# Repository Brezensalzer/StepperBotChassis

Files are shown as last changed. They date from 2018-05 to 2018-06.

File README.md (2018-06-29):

# StepperBotChassis

This is the chassis of a two wheeled rover with stepper motors for 
precision movement. It is part of a larger project. The whole rover is 
"layered" in three slices:

- the chassis layer: https://github.com/Brezensalzer/StepperBotChassis
- the control layer: https://github.com/Brezensalzer/StepperBotController
- the sensor layer: https://github.com/Brezensalzer/StepperBotLidar2
- the ground station code: https://github.com/Brezensalzer/StepperBotGroundStation

The Arduino code is for a Teensy LC but should be easily adaptable to 
other microcontroller boards. Openscad, FreeCAD drawings and STL files 
are provided for 3D printing.

The chassis works great on a smooth floor (parquet) but on the seams of 
floor tiles it is easily pushed off track because of the small ball 
caster.

To complete the mechanical build, the following parts are needed:

- 2x Pololu DRV8834 Low-Voltage Stepper Motor Driver Carrier
- 2x Stepper motor 11HS12-0674S
- 2x O-rings 60 x 5 mm
- 2x 18650 LiPo cell
- LiPo protection circuit
- LiPo charging module
- Pololu ball caster 3/8" plastic ball
- Pololu 3.3V step-up/step-down voltage regulator S7V8F3
- Teensy LC
- Toggle switch 3-pin
- M2.5 screws for the stepper mounting

<p align="center">
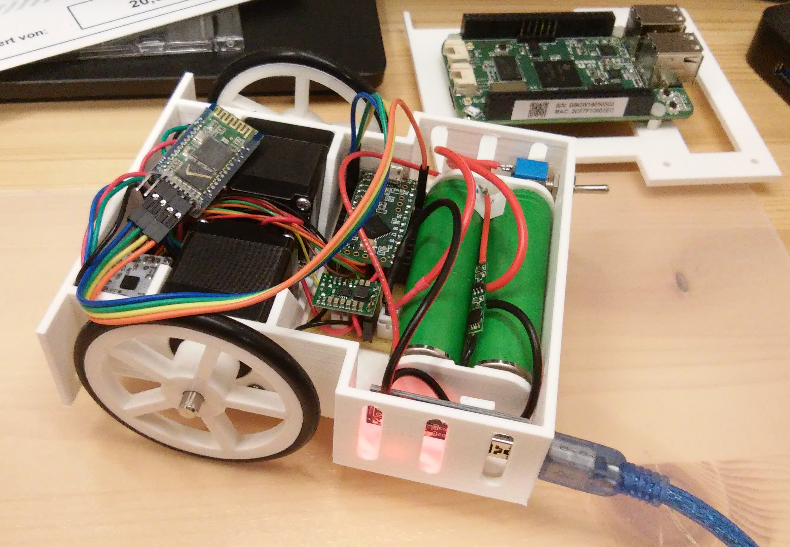
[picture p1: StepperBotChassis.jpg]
  
</p>

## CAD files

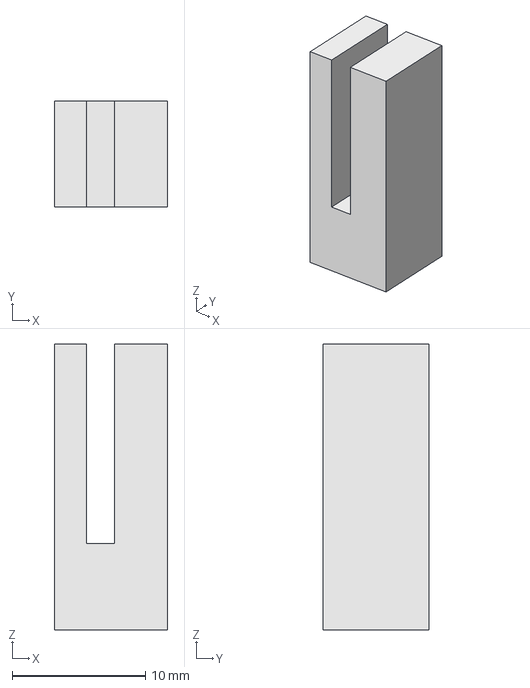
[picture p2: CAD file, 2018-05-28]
3D_parts/ChargerSockel.fcstd
8.50 x 8.00 x 21.5 mm

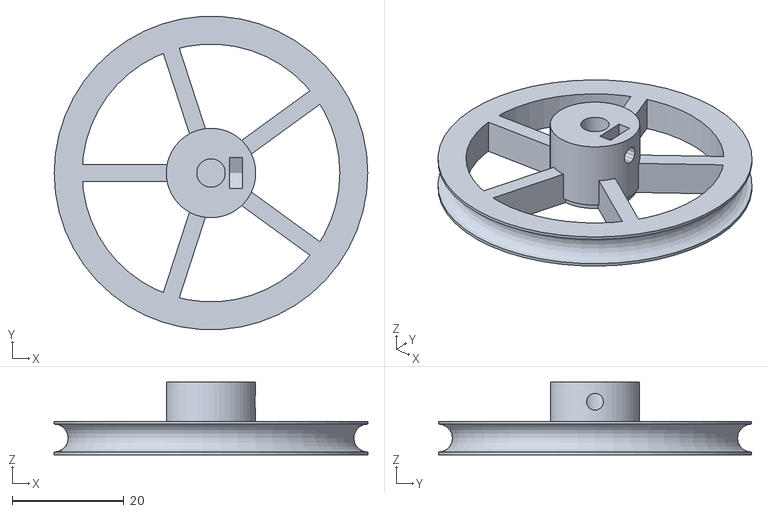
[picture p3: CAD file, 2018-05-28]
3D_parts/Wheel.stl
56.1 x 56.0 x 13.0

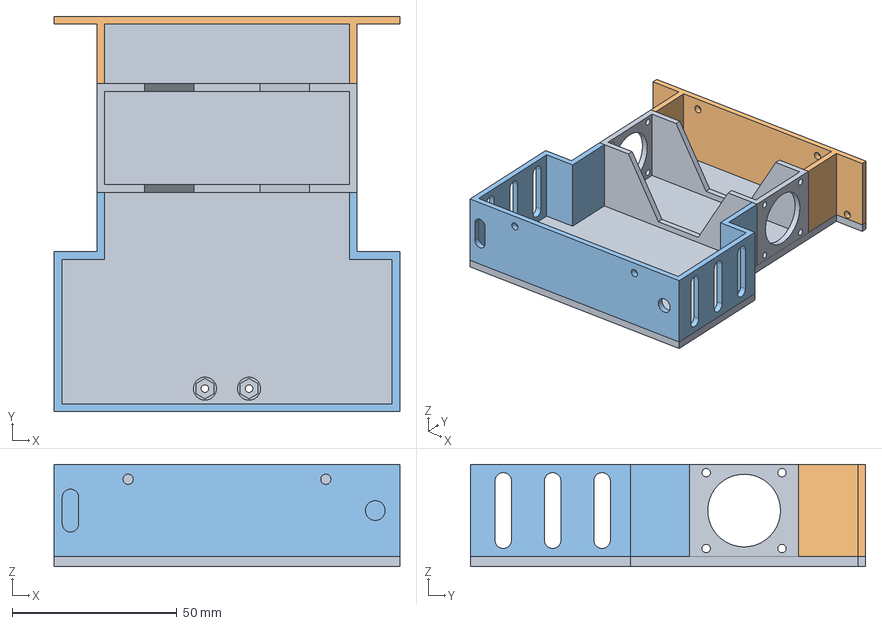
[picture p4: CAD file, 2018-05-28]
3D_parts/ChassisBase.FCStd
105.0 x 120.0 x 31.0 mm

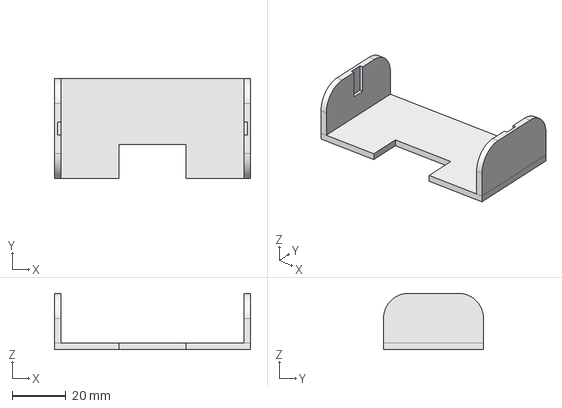
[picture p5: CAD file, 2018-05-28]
3D_parts/Batteriesockel.fcstd
72.6 x 37.0 x 20.9 mm

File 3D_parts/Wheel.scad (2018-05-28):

/*
 * Highly Configurable Wheel (One Wheel To Rule Them All)
 *
 * by Alex Franke (CodeCreations), Apr-Jun 2012
 * http://www.theFrankes.com
 * 
 * Licenced under Creative Commons Attribution - Non-Commercial - Share Alike 3.0 
 * 
 * INSTRUCTIONS: Choose some values in the "User-defined values" section, render, print, smile
 *     broadly, share with friends, and send the author a few bottles of your favorite beer. 
 * 
 * CREDITS: Center-trapped nut/bolt design inspired by Wade's Geared Extruder 
 *     (http://www.thingiverse.com/thing:1794). The spiral spoke design was apparently designed in 
 *     parallel with tjhowse's Parametric airless tire (http://www.thingiverse.com/thing:17514), and 
 *     although it can be configured to act in a very similar way, it was originally designed to be 
 *     a rigid spoke design. Vane code by JoeyC (JEC).
 *       Some features were inspired or suggested by commenters. I'll try to add credits in the code
 *     for those features. 
 * 
 * v1.33, Oct 16, 2012: Added code to generate vanes for use with slot detectors.  JEC
 * v1.32, Jun 9, 2012: Fixed a bug that cause outer nut trap to not render properly. 
 * v1.31, Jun 9, 2012: Fixed a bug that didn't include shaft flats when rendered without a hub.
 * v1.30, Jun 9, 2012: Features requested by JuliaDee: Added option for v-grooves instead of just 
 *     o-rings; Added flatted shaft option. 
 * v1.23, Apr 23, 2012: Fixed a bug that places the trapped nuts incorrectly, without considering 
 *     shaft size. Added a parameter to offset the placement of these nuts. (Thanks, AUGuru, for both 
 *     of these!) 
 * v1.22, Apr 21, 2012: Added credits section to instructions. Fixed some argument/reference issues. 
 *     Better knob foundation calculation/rendering. Fixed a number of bugs in knob sizing, including 
 *     the bug indetified by TakeItAndRun, where the knobs sometimes extend into the interior of the 
 *     wheel. 
 * v1.21, Apr 18, 2012: Fixed bug that prevented timing holes from rendering properly with spoke
 *     inset. Edited comments a bit and cleaned up some code. Combined a few parameters.
 * v1.20, Apr 17, 2012: Line style uses spokeWidth. Supports an inner circle using innerCircleDiameter. 
 *     Cleaned up some unnecessary code. Added spokeInset to allow seperate sized of rim and rest of
 *     wheel. Added captive nut option in hub. Added convexity of spoke area (inner and outer).
 * v1.10, Apr 16, 2012: Hub now supports standard hobby servo mounting arms/horns. Renders flat.
 * v1.00, Apr 15, 2012: Initial release. This is a combination of several other several other 
 *     wheel designs that all used the same framework, including http://www.thingiverse.com/thing:21277
 *     http://www.thingiverse.com/thing:21065, http://www.thingiverse.com/thing:21064, and 
 *     http://www.thingiverse.com/thing:21010, as well as some parts of my encoder wheel design at 
 *     http://www.thingiverse.com/thing:20491. I should be finishing my taxes right now. 
 *
 * TODO: 
 *   * Call wheel() with arguments (so it's more library-like)
 *   * Triangle spoke style
 *   * Gear tooth "tread" pattern
 *   * Bearing retainer (AUGuru)
 *   * perhaps move content of rim() to where the rim is actually built so inner hole can be punched out
 *   * outer hub styles (TakeItAndRun)
 */

/////////////////////////////////////////////////////////////////////////////
// User-defined values... 
/////////////////////////////////////////////////////////////////////////////

// Tire Parameters:
//      Often wheels are built around the tires. In this section, specify the properties of the 
//   tires you're using, and this will define the diameter of the wheel. If you're using o-rings, 
//   the tireCSDiameter should be the cross-section diameter of the o-ring, or if you're using some
//   other flat tire material (such as rubber bands), jsut specify the its thickness. If you're not
//   using any tire at all, set the tireCSDiameter to zero. 

wheelWidth     = 6;     // The width (or thickness) of the wheel at the rim.
tireCSDiameter = 5;     // Cross-sectional diameter (CS) -- How thick is the tire rubber?
tireID         = 50;    // Internal diameter (ID) -- How wide is the inside opening? 
tireStretch    = 1.02;  // Circumferential stretch percentage (usually 1 + 0-5%, e.g. 1.02) -- How 
                        //   much do you want to stretch it to get it on? 

// Rim properties 
//      The rim sits at at the outside of the spokes and supports the tires or added treads. 
//   Installed tires (such as o-rings, rubber bands, etc) are set into grooves carved out of the
//   rim, while trads are added onto it. Keep this in mind when you're using tires -- as an 
//   example, the rim height should not be smaller than the radius of o-ring tires. 
//      The rim also supports rotary encoder timing holes for wheel feedback. Use the padding 
//   parameters to adjust the location of those holes. See the compiler output for helpful 
//   information about the distance indicated by each timing hole. Directional timing holes 
//   will produce a second set of holes that are 90 degrees out of phase with the first. This 
//   allows you to stack sensors at the same location over the wheel instead of trying to 
//   position them along the circumference. Directional timing holes essentially double the 
//   resolution. You can also double resolution by looking for both rising and falling edges. 

rimHeight      = 5;        // The height of the rim portion of the wheel. 
timingHoles    = 0;        // The number of timing holes to carve into the rim
timingHolePad  = [1,0.5,3]; // The [inside,middle,outside] padding for the timing holes
directional    = false;      // A directional encoder renders two sets of slots, 90 deg out of phase

// Added 10/16/2012 JEC
// Slot detector vane properties
// These settings generate small vanes on the inside of the rim for use with
// IR slot detectors that are too narrow to be put over the wheel.
vaneCount		= 0;			// Number of slot detector vanes to put inside rim
vaneHeight		= 7;			// The height of the vanes
vaneWidth		= 1;			// Width of vanes
vaneLength		= 4;			// Length of vanes
vaneOffset		= 1;			// Offset into wheel of vanes
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

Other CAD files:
3D_parts/Batteriesockel.stl
3D_parts/ChargerSockel.stl
3D_parts/ChassisBase.stl

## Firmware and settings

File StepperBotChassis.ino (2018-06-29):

// StepperBotChassis.ino
//
//    Wiring
//
//    Function          Teensy LC             Beaglebone green
//    ---------------   ---------------       -----------------
//    serial            Pin 0 (RX1)           P9-13 (UART4_TXD)
//    serial            Pin 1 (TX1)           P9-11 (UART4_RXD)
//    emergency break   Pin 3 (Input, pullup) P9-15 (GPIO_48, Output)
//    DRV8834 sleep     Pin 4 (Output)        -
//    M0 Microstepping  Pin 5 (Output)        -
//    M1 Microstepping  Pin 6 (Output)        -
//    step right        Pin 7 (Output)        -
//    dir right         Pin 8 (Output)        -
//    step left         Pin 9 (Output)        -
//    dir left          Pin 10 (Output)       -

#include <AccelStepper.h>
#include <MultiStepper.h>

// sleep/enable pin
#define SLEEP_PIN 4
// microstep control for DRV8834
#define M0 5
#define M1 6
// All the wires needed for full functionality
#define STEP_RIGHT 7
#define DIR_RIGHT 8
#define STEP_LEFT 9
#define DIR_LEFT 10
#define EMERGENCY_PIN 3

// global variables
int   stepperSpeed = 400;   // speed of the stepper (steps per second)
float wheel_dia = 61.0;      // # mm (increase = spiral out)
float wheel_base = 105.2;    // # mm (increase = spiral in) 
int   steps_rev = 200;      // steps per revolution
long positions[2];
long steps1, steps2, delta;
int gear = 1;
   
// Serial Com
const char del = '#';     // delimiter
int  num;           // bytes received
char cmd;           // command
int  cmdFloat;      // command value as float
String command;

AccelStepper stepperLeft(AccelStepper::DRIVER, STEP_LEFT, DIR_LEFT);
AccelStepper stepperRight(AccelStepper::DRIVER, STEP_RIGHT, DIR_RIGHT);

// Up to 10 steppers can be handled as a group by MultiStepper
MultiStepper steppers;

void setup() {
  // serial com
  Serial1.begin(9600);
  Serial1.flush();
  Serial1.setTimeout(10000); 
  
  // set power on/off pin
  stepperLeft.setEnablePin(SLEEP_PIN);
  stepperRight.setEnablePin(SLEEP_PIN);

  //set target motor speed steps/s.
  stepperLeft.setMaxSpeed(stepperSpeed);
  stepperRight.setMaxSpeed(stepperSpeed);
  
  // set full steps and enable driver
  // M0 = low, M1 = low
  pinMode(M0, OUTPUT);
  digitalWrite(M0, LOW);
  pinMode(M1, OUTPUT);
  digitalWrite(M1, LOW);
  pinMode(SLEEP_PIN, OUTPUT);
  digitalWrite(SLEEP_PIN, HIGH);

  // Then give them to MultiStepper to manage
  steppers.addStepper(stepperLeft);
  steppers.addStepper(stepperRight);

  // energy saving
  enableOutput(false);

  // emergency stop
  pinMode(EMERGENCY_PIN, INPUT_PULLUP);
}

void loop() {
  // reset variables
  command = "";
  num = 0;
  cmd = 'X';

  // read and parse command
  command = Serial1.readStringUntil(del);
  
  if (command != "") {
    cmd = command.charAt(0);
    num = command.indexOf(del);
    command = command.substring(1,num);
    cmdFloat = command.toFloat();

    // execute command
    switch (cmd) {
      // enable output
      case 'e':
        enableOutput(true);
        break;
      // disable output
      case 'd':
        enableOutput(false);
        break;
      // forward
      case 'f':
        forward(cmdFloat);
        break;
      // backward
      case 'b':
        backward(cmdFloat);
        break;
      // turn left
      case 'l':
        left(cmdFloat);
        break;
      // turn right
      case 'r':
        right(cmdFloat);
        break;
      // set stepper speed
      case 's':
        stepperSpeed = command.toInt();
        break;
      // set wheel diameter
      case 'w':
        wheel_dia = cmdFloat;
        break;
      // set wheel track width
      case 't':
        wheel_base = command.toFloat();
        break;
      // debug info
      case 'i':
        Serial1.println("$Id$");
        Serial1.print("wheel diameter: ");
        Serial1.println(wheel_dia);
        Serial1.print("wheel_base: ");
        Serial1.println(wheel_base);
        Serial1.print("stepperSpeed: ");
        Serial1.println(stepperSpeed);
        break;
      default:
        Serial1.println("error");
        break;
      }
    Serial1.println("ok");
    Serial1.flush(); 
  }
  
}

// ----- HELPER FUNCTIONS -----------
int step(float distance){
  int steps = distance * steps_rev / (wheel_dia * 3.1412);
  //Serial1.print("calculated steps: ");
  //Serial1.println(steps);
  return steps;  
}

void enableOutput(boolean flag){
  if(flag){
    // wakeup steppers
    stepperLeft.enableOutputs();
    stepperRight.enableOutputs();    
  }
  else{
    // energy saving
    stepperLeft.disableOutputs();
    stepperRight.disableOutputs();    
  }
}

void emergencyStop(){
  if(digitalRead(EMERGENCY_PIN) == LOW){
    stepperLeft.stop();  
    stepperRight.stop();
  }
}

void forward(float distance){
  gear = 1;
  positions[0] = step(distance);  
  positions[1] = positions[0];
  steps1 = positions[0];
  steppers.moveTo(positions);
  stepperLeft.setSpeed(stepperSpeed/4);
  stepperRight.setSpeed(-stepperSpeed/4);
  while (steps1 > 0) {
    emergencyStop();
    steps1 = stepperLeft.distanceToGo();
    steps2 = stepperRight.distanceToGo();
    // poor man's acceleration
    delta = positions[0] - steps1;
    if ((delta >= 10) && (delta < 50))
      {
        if (gear == 1) {
          stepperLeft.setSpeed(stepperSpeed/2);
          stepperRight.setSpeed(-stepperSpeed/2);
          gear = 2;
        }
       }
    else if ((delta >= 50) && (steps1 > 50))  
      {
        if (gear == 2) {
          stepperLeft.setSpeed(stepperSpeed*3/4);
          stepperRight.setSpeed(-stepperSpeed*3/4);
          gear = 3;
        }
       }
    else if ((delta >= 100) && (steps1 > 100))  
      {
        if (gear == 3) {
          stepperLeft.setSpeed(stepperSpeed);
          stepperRight.setSpeed(-stepperSpeed);
          gear = 4;
        }
       }
    // deceleration   
    else if ((steps1 <= 100) && (steps1 > 50))   
      {
        if (gear == 4) {
          stepperLeft.setSpeed(stepperSpeed/2);
          stepperRight.setSpeed(-stepperSpeed/2);
          gear = 3;
        }
       }
    else if ((steps1 <= 50) && (steps1 > 10))   
      {
        if (gear == 3) {
          stepperLeft.setSpeed(stepperSpeed/2);
          stepperRight.setSpeed(-stepperSpeed/2);
          gear = 2;
        }
       }
    else if (steps1 <= 10)   
      {
        if (gear == 2) {
          stepperLeft.setSpeed(stepperSpeed/4);
          stepperRight.setSpeed(-stepperSpeed/4);
          gear = 1;
        }
       }
    steppers.run();
  }
  stepperLeft.setCurrentPosition(0);
  stepperRight.setCurrentPosition(0);
}

void backward(float distance){
  gear = 1;
  positions[1] = step(distance);  
  positions[0] = positions[1];
  steps2 = positions[1];
  steppers.moveTo(positions);
  stepperLeft.setSpeed(-stepperSpeed/4);
  stepperRight.setSpeed(stepperSpeed/4);
  while (steps2 > 0) {
    emergencyStop();
    steps1 = stepperLeft.distanceToGo();
    steps2 = stepperRight.distanceToGo();
    // poor man's acceleration
    delta = positions[1] - steps2;
    if ((delta >= 10) && (delta < 50))
      {
        if (gear == 1) {
          stepperLeft.setSpeed(-stepperSpeed/2);
          stepperRight.setSpeed(stepperSpeed/2);
          gear = 2;
        }
       }
    else if ((delta >= 50) && (steps2 > 50))  
      {
        if (gear == 2) {
          stepperLeft.setSpeed(-stepperSpeed*3/4);
          stepperRight.setSpeed(stepperSpeed*3/4);
          gear = 3;
        }
       }
    else if ((delta >= 100) && (steps2 > 100))  
      {
        if (gear == 3) {
          stepperLeft.setSpeed(-stepperSpeed);
          stepperRight.setSpeed(stepperSpeed);
          gear = 4;
        }
       }
    // deceleration   
    else if ((steps2 <= 100) && (steps2 > 50))   
      {
        if (gear == 4) {
          stepperLeft.setSpeed(-stepperSpeed/2);
          stepperRight.setSpeed(stepperSpeed/2);
          gear = 3;
        }
       }
    else if ((steps2 <= 50) && (steps2 > 10))   
      {
        if (gear == 3) {
          stepperLeft.setSpeed(-stepperSpeed/2);
          stepperRight.setSpeed(stepperSpeed/2);
          gear = 2;
        }
       }
    else if (steps2 <= 10)   
      {
        if (gear == 2) {
          stepperLeft.setSpeed(-stepperSpeed/4);
          stepperRight.setSpeed(stepperSpeed/4);
          gear = 1;
        }
       }
    steppers.run();
  }
  stepperLeft.setCurrentPosition(0);
  stepperRight.setCurrentPosition(0);
}

void right(float degrees){
  float rotation = degrees / 360.0;
  float distance = wheel_base * 3.1412 * rotation;
  positions[0] = step(distance);  
  positions[1] = positions[0];
  steps1 = positions[0];
  steppers.moveTo(positions);
  stepperLeft.setSpeed(stepperSpeed/4);
  stepperRight.setSpeed(stepperSpeed/4);
  while (steps1 > 0) {
    steps1 = stepperLeft.distanceToGo();
    steps2 = stepperRight.distanceToGo();
    steppers.run();
  }
  stepperLeft.setCurrentPosition(0);
  stepperRight.setCurrentPosition(0);
}

void left(float degrees){
  float rotation = degrees / 360.0;
  float distance = wheel_base * 3.1412 * rotation;
  positions[0] = -step(distance);  
  positions[1] = positions[0];
  steps1 = positions[0];
  steppers.moveTo(positions);
  stepperLeft.setSpeed(-stepperSpeed/4);
  stepperRight.setSpeed(-stepperSpeed/4);
  while (abs(steps1) > 0) {
    steps1 = stepperLeft.distanceToGo();
    steps2 = stepperRight.distanceToGo();
    steppers.run();
  }
  stepperLeft.setCurrentPosition(0);
  stepperRight.setCurrentPosition(0);
}

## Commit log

2018-05-28 imported project
    [Batteriesockel.fcstd, Batteriesockel.stl, ChargerSockel.fcstd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]
2018-06-14 updated README.md with link to ground station code
2018-06-29 changed stepper driver to full steps
2018-06-29 corrected part number of voltage regulator
